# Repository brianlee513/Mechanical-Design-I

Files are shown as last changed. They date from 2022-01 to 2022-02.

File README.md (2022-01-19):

# Mechanical-Design-I
ME 370

The goal of this project is to design and build a four legged walker with two different mechanisms. 
More specifically, linkage design and cam follower design. With a single motor given, the four leggeed walker should be capable of walking 10m under 2 minutes.

The side view of the final design



Mechanism of the Rear Legs ( Cam Follower Design)



Mechanism of the Front Legs (Linkage Design)



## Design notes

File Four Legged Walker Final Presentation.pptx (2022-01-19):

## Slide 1

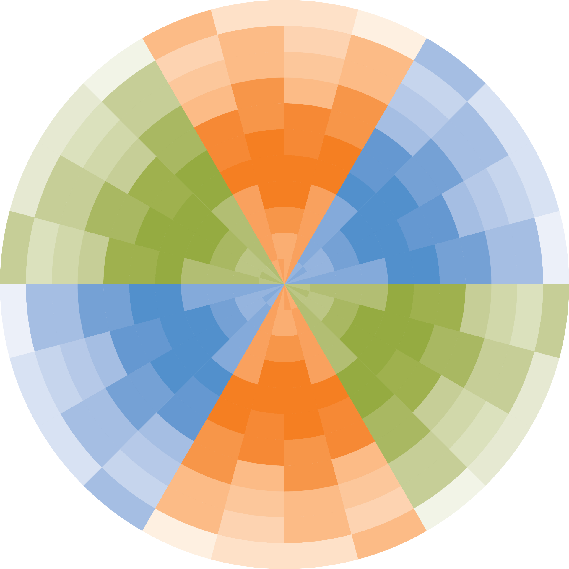
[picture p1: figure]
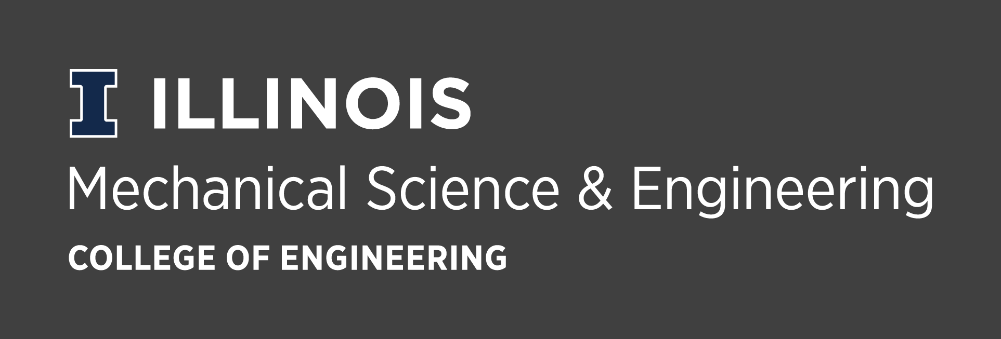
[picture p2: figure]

ME370
4-Legged Walker Final Report

Team 12:
Josh Stutzman, Marco Gasca, Brian Lee, Shubh Taneja
Section:
Date: 12/3/2021

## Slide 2

Overview

- 4 bar Linkage Design
- Slot Cam Design
- Power Source: 4 AA Batteries & DC Motor
- 2 Belts Transmit power
- 3 Gears in Total
( 30T Gear, 24T Gear )

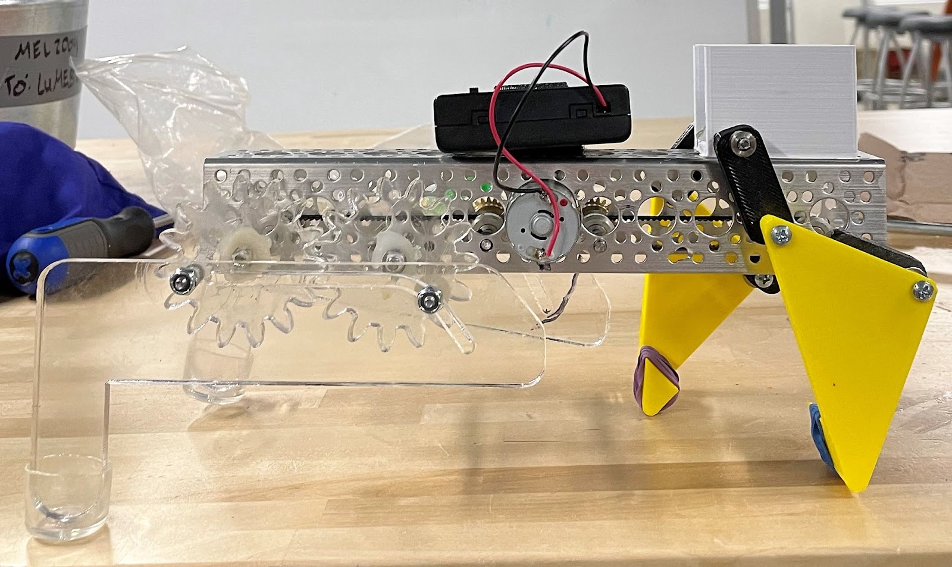
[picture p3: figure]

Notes: General Theme: legs closer to the u-base and have minimal parts to accomplish the goal.
Having many parts builds up movements creating unstable walker.

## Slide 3

Power Transmission Unit

Side View

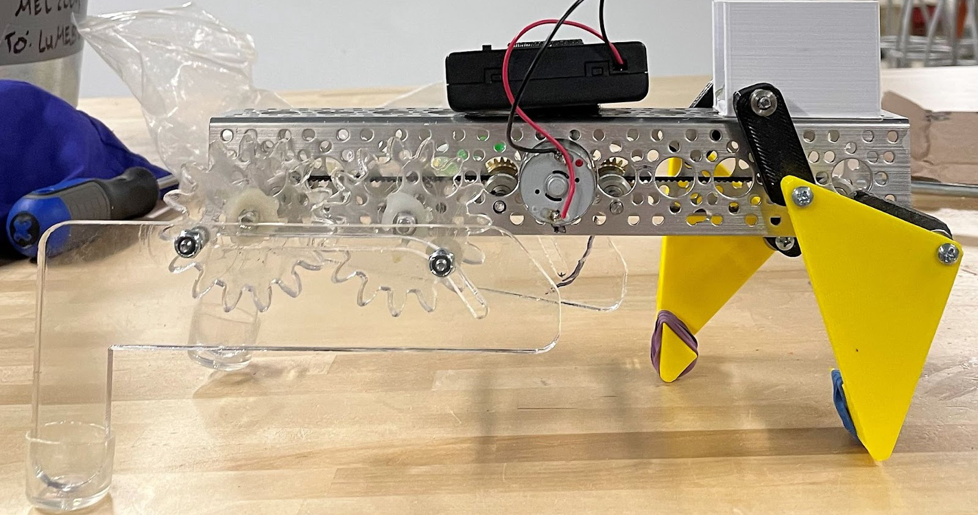
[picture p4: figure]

Rear Leg (Axial Translating Flat Form Closure)

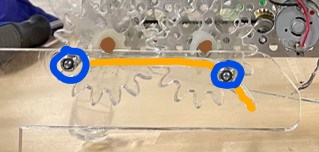
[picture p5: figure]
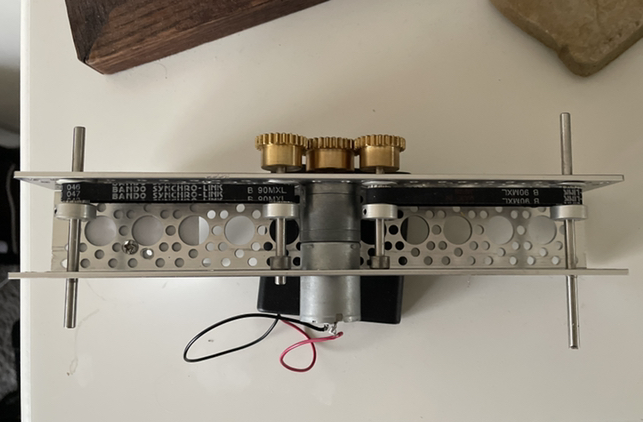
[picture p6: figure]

Bottom View 1

Bottom View 2

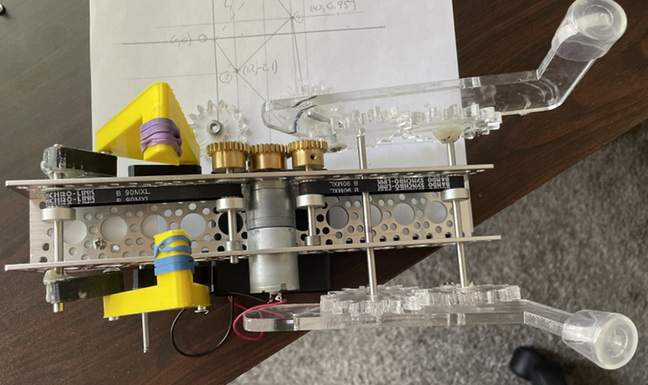
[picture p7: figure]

Front Leg

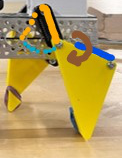
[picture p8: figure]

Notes: The transmission unit consists of one 30t gear, two 24t gears, two belts that transmit the rotational movement to the end of the u-base, and four shafts.
Rigid Link: provided the desired foot path, while keeping the legs closer to the u-base.
Cam-Follower: this type of design provided us to accomplish both vertical and horizontal motion of the leg at the same time.

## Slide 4

Foot Path

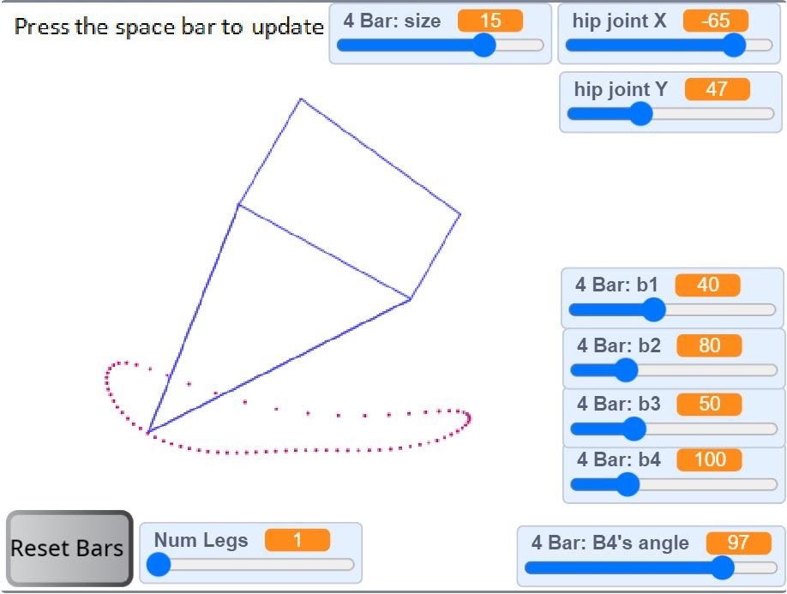
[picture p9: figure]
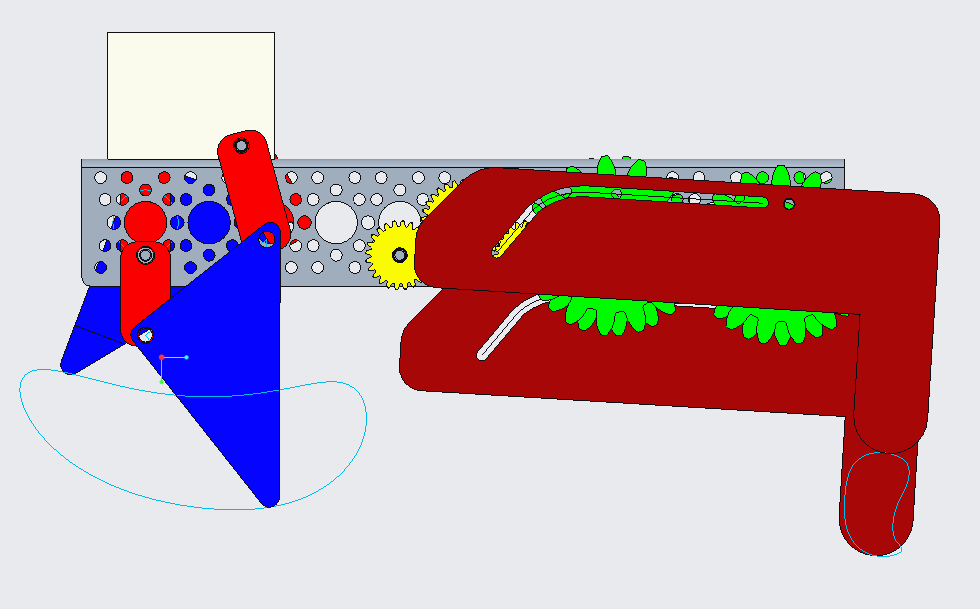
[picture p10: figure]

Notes: Front leg has some flaws where it’s a quick return.
The pros for the rear leg is that it is not a quick return. It makes the step very stable and uniform.

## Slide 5

Speed of the Walker

Load | 0g | 300g | 450g | 600g | 712.5g
RPM of DC Motor | 116.86 | 106.58 | 101.94 | 98.19 | 94.07
RPM 30T Gear | | | | | 94.07
RPM 24T Gear | | | | | 117.5828

- Step Size : Approximately 8 cm/rotation
- Calculated Speed : 13.7 cm/s
- Approximately 90s to complete 12m

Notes: From the DC motor lab, we calculated the approximated rpm for the motor, 30T gear, and 24t gear by applying the weight(712.5g) of the walker as the load.
Then calculated the actual speed of the walker. However, the actual speed of the walker differs quite significantly due to slipping and imbalance of the u-base creating the foot path to lose or make contact earlier than expected.

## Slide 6

PVA and DFA Analysis of Rigid Linkage Leg Animation

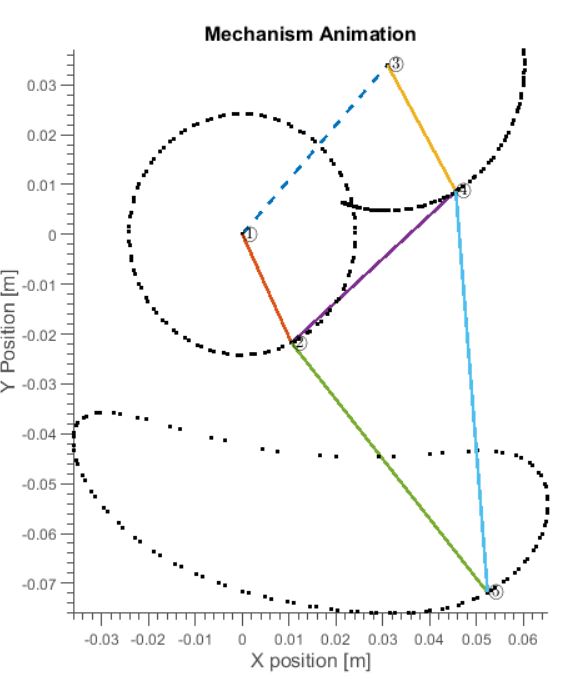
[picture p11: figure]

- Contact time- 60%
- Stride Length Ls – 8cm

Lift Phase

Contact Phase

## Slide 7

PVA and DFA Analysis of Rigid Linkage Leg

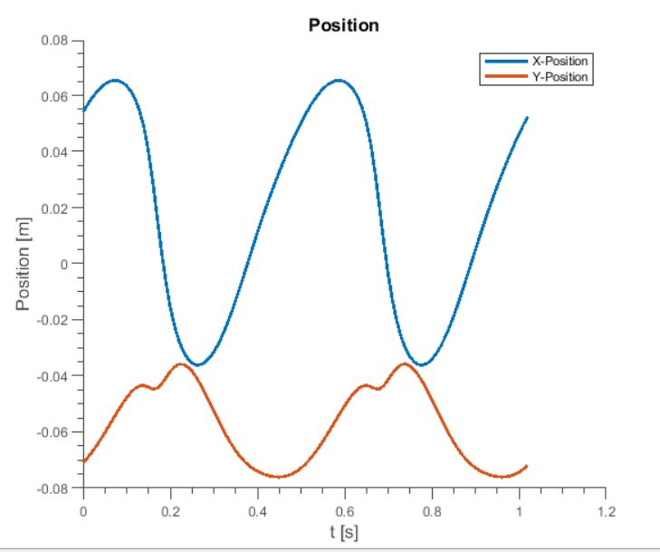
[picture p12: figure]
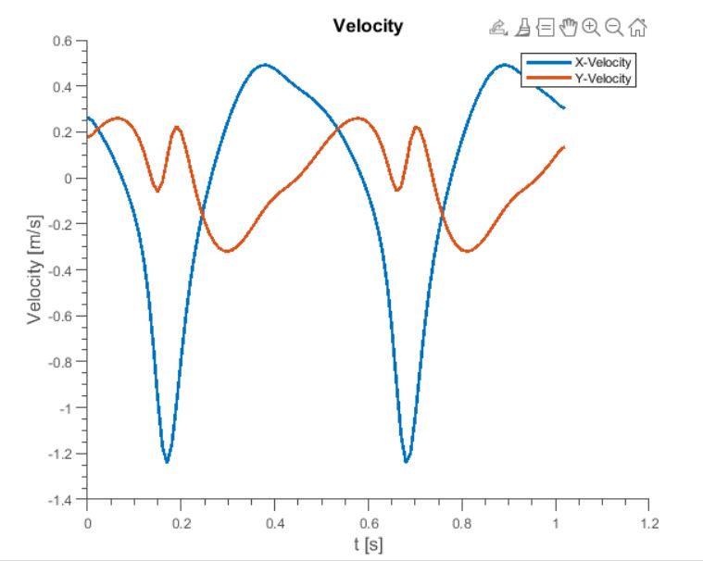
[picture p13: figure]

Contact Phase

Lift Phase

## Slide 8

PVA and DFA Analysis of Rigid Linkage Leg

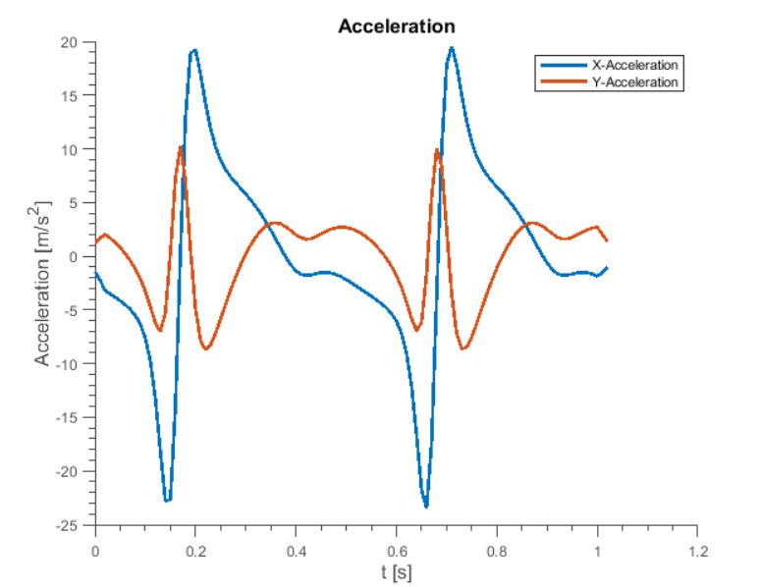
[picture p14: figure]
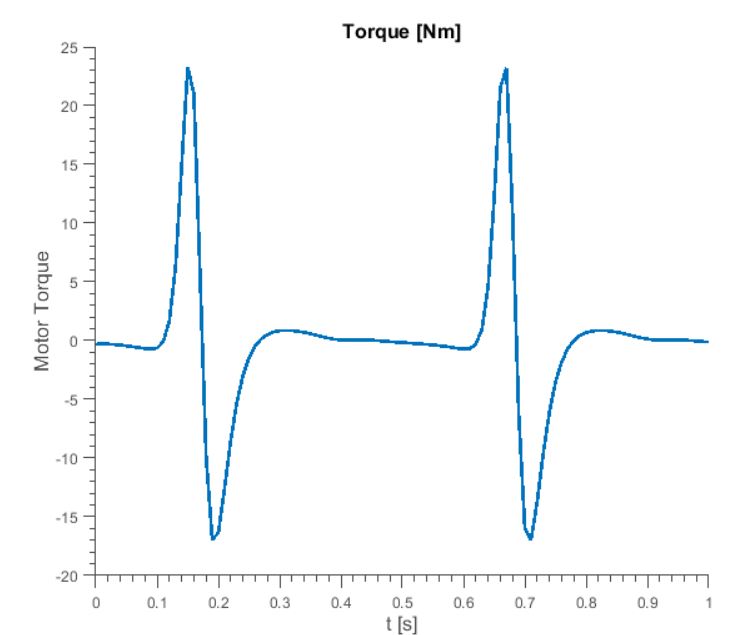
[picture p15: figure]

Contact Phase
Valid
Max Torque = -0.5Nm

Lift Phase
Invalid

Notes: Acceleration was abnormally high for some unknown reason. The torque was very low except for the spikes which can be ignored.

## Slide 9

Exploded View and Engineering Drawings

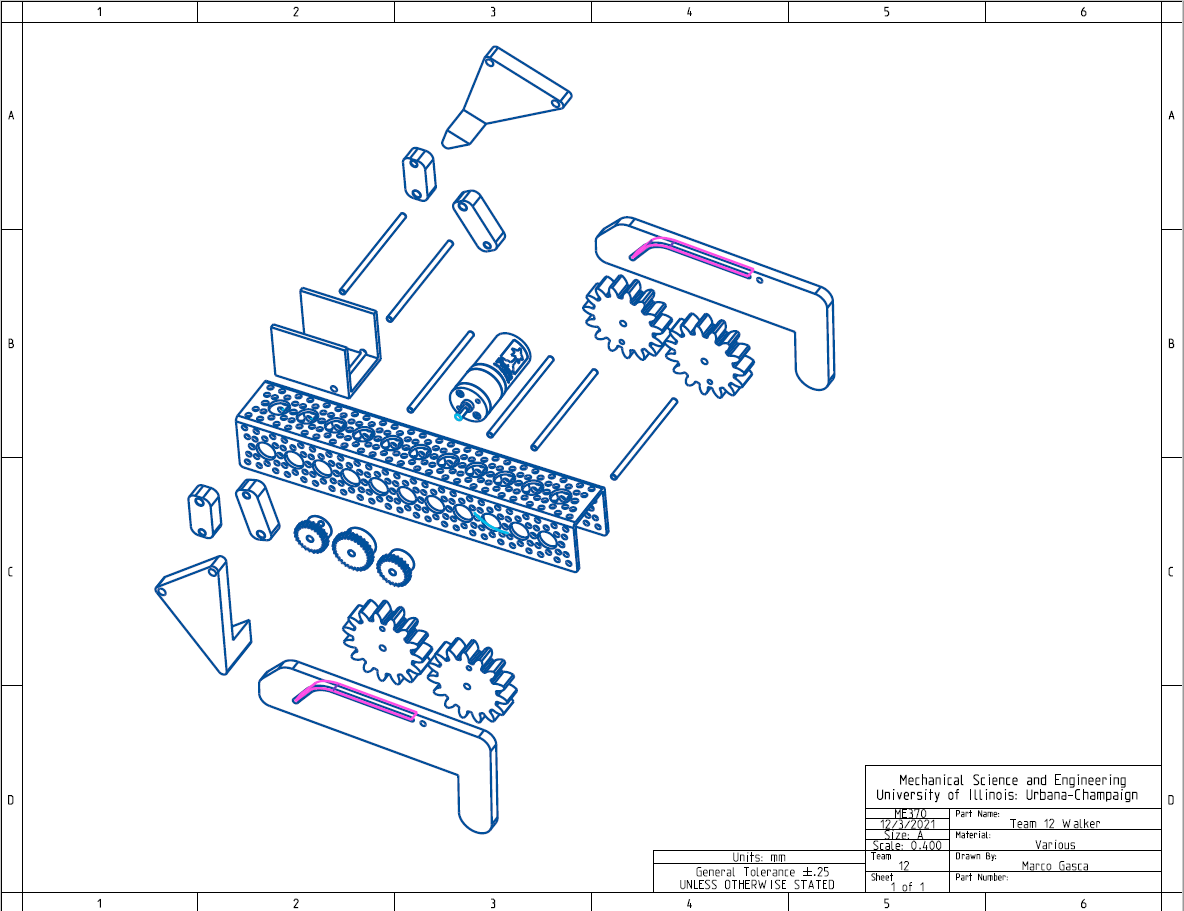
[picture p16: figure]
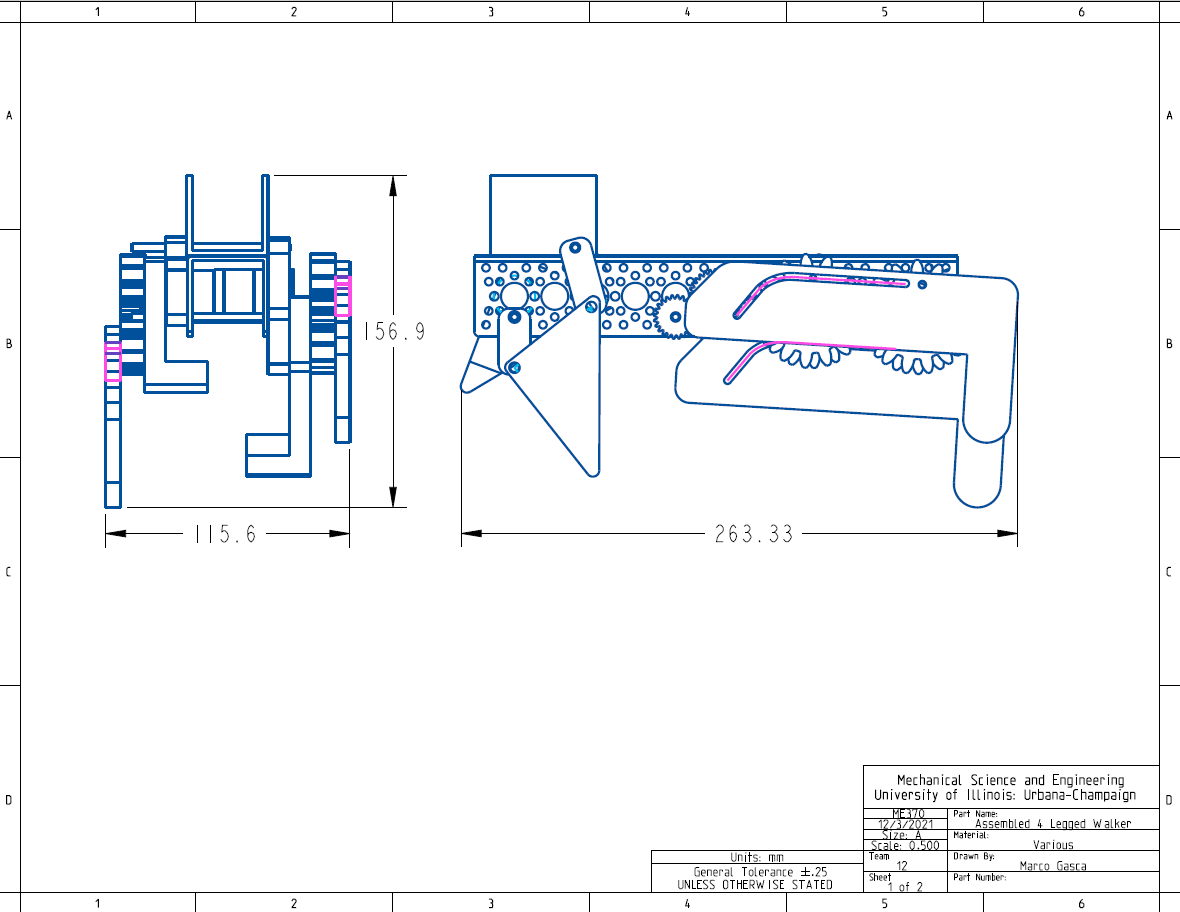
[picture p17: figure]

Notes: The transmission unit consists of one 30t gear, two 24t gears, two belts that transmit the rotational movement to the end of the u-base, and four shafts.

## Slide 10

Budget and Bill of Materials

Cost Breakdown
Part | Quantity | Unit Cost ($) | Total Cost ($) | Part | Quantity | Unit Cost ($) | Total Cost ($)
U-base | 1 | 8 | 8 | Allen Wrench 1.27 mm | 1 | 0.2 | 0.2
DC Motor | 1 | 20 | 20 | Allen Wrench 1.5 mm | 1 | 0.2 | 0.2
24 Tooth Gear | 2 | 23.4 | 46.8 | Sleeve Bearing | 1 | 0.6 | 0.6
30 Tooth Gear | 1 | 25.2 | 25.2 | #6-32 Coarse Nut | 6 | 0.32 | 1.92
Batteries and Accessories | 1 | 22 | 22 | #6-32 ½” Machine Screw | 2 | 0.21 | 0.43
Belt Gear 15 Tooth | 4 | 14.6 | 58.4 | #6-32 ¾” Machine Screw | 4 | 0.21 | 0.85
182 mm Belt | 2 | 5.5 | 11 | Barrel Nut and Screw ⅞” | 4 | 0.5 | 2
Shaft Collar | 14 | 1.7 | 23.8 | Acrylic Sheet 24” x 12” x ¼” | 1 | 20 | 20
150 mm Shaft | 2 | 1.2 | 2.4 | ¼” x 36” steel rod | 1 | 3.4 | 3.4
50 mm Shaft | 2 | 1 | 2 | ⅞” Clear Leg Tip | 2 | 0.7 | 1.41
73 mm Shaft | 1 | 0.6 | 1.2 | 3D Printed Leg | 63g | 0.03 | 1.89
#10 Washers | 4 | 0.04 | 0.16 | 3D Printed U-base Extension | 17g | 0.03 | 0.51

Sum | | 1 | 220.96 | | | 2 | 33.41
Total Cost | | | | | | 1 + 2 | 254.37

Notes: Most of the cost comes from the body of the walker- motor, gears, belts and batteries. The prototype legs themselves were very cheap and did not contribute much to the total cost. The total cost of the rocker is under budget, but enough of the budget was used to ensure that corners weren’t cut and a quality product was produced.

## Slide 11

Design Failures / Lesson Learned

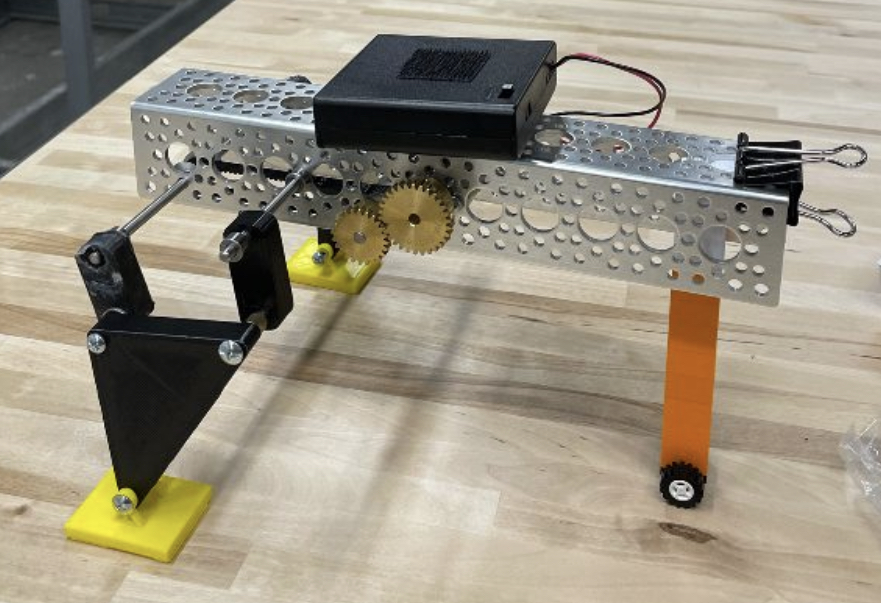
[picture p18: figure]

Linkage Design 1

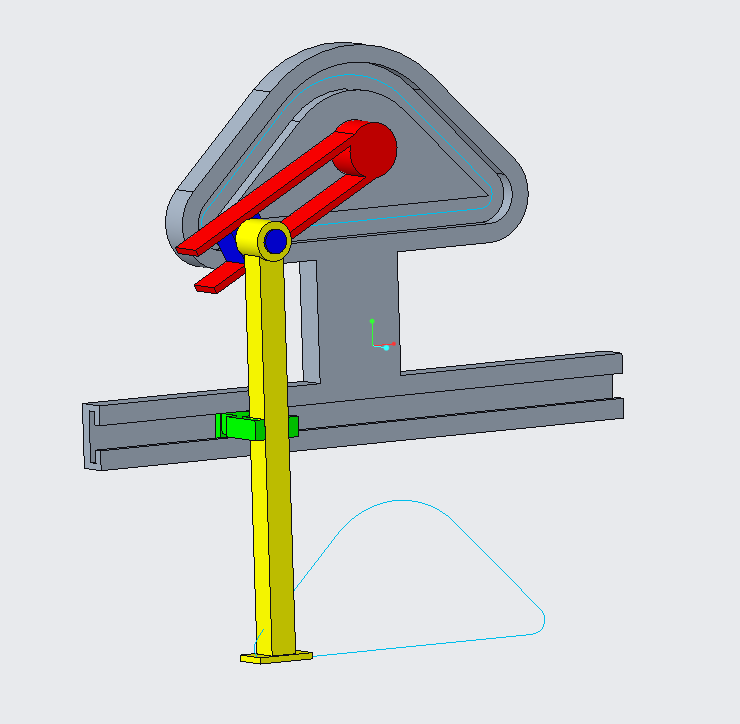
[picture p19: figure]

Cam Design 1

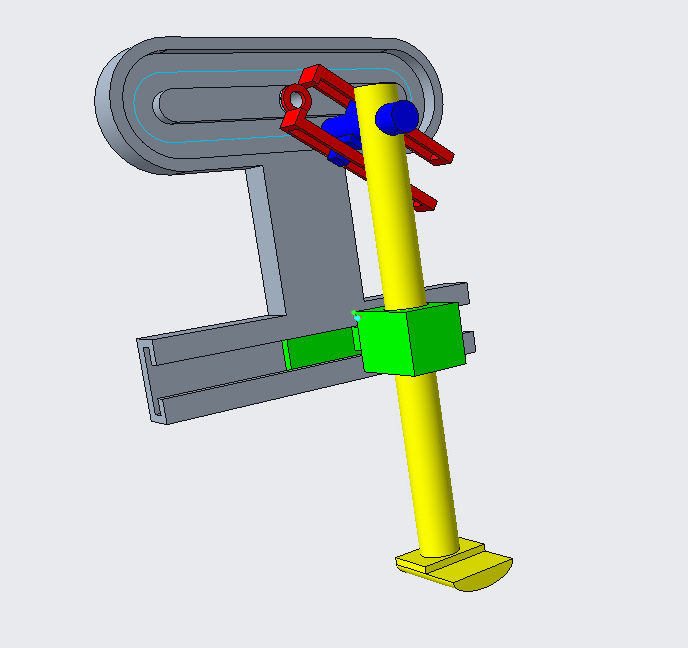
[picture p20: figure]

Cam Design 2

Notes: Design Iterations
Design1: The legs were too far out from the u-base. Single point contact for the rear wheel.
Cam Design 1:
Uncertainty over how the mechanism will behave at the sharp corners.
Nothing was holding the blue follower and the yellow leg to fall out of the slot.
The green clamp rotated as the blue follower lead the motion, making the mechanism to lock at one location
Cam Design 2:
Since the Red part is leading the motion, there was a delay in motion at the green slider. The delay created the yellow piece to be out of its perpendicular position to the ground.

Lesson Learned:
Designing: Considering fastening methods at the earlier stage
Manufacturing: Considering manufacturing challenges in 3d printing, long wait and tolerance issue
Testing: Considering the method of testing after manufacturing. Supply and the level of test we desire.
Right supply to keep one end for the u-base to maintain horizontal. The desired footpath was generated, but the foot was hitting the ground earlier than expected because the rear was lowered than the front.

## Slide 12

Progression Video

https://drive.google.com/file/d/1e48WqrADJp_-YnRn2FuT256TExa1mEri/view?usp=sharing

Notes: Just to be displayed on screen

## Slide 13

Team Contributions

- Design Review:
  - Marco Gasca: Measured possible hole to be utilized
  - Brian Lee: 3d modeling of the entire walker with the chosen design, Calculated the linkage
  - Josh Stutzman: Path generation for both legs
  - Shubh Taneja: Assisted in path generation
- Milestone 1:
  - Marco Gasca: 3D printed the CAD parts
  - Brian Lee: Create CAD model of all the linkage parts and designed linkage
  - Josh Stutzman: Assembled the linkage design, and tested
  - Shubh Taneja: Brainstormed and suggested possible linkage designs
- Milestone 2:
  - Marco Gasca: Create CAD model for the cam-follower design
  - Brian Lee: Assisted in creating cam-follower design, laser cut the parts, and tested the walker
  - Josh Stutzman: Assembled the cam-follower design, tested the walker, and assisted in design
  - Shubh Taneja: No contribution
- Deliverables 2 & 3:
  - Marco Gasca: CAD rendering and assembly engineering drawings (Part 4)
  - Brian Lee: Design description and analysis (Part 1)
  - Josh Stutzman: PVA and DFA analysis and budget and BOM (Parts 2 & 3)
  - Shubh Taneja: 1-minute video

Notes: Just to be displayed on screen

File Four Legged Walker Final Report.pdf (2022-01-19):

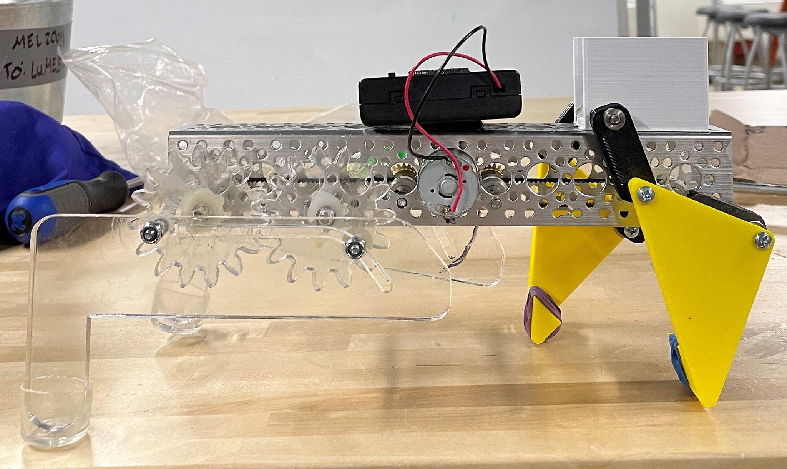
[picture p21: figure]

# Detailed Design Report

# ME 370 Section CB3 Team 12

Josh Stutzman, Marco Gasca, Brian Lee, Shubh Taneja

December 6, 2021

## Abstract

The purpose of this walker team project is to construct a four-legged walker that’s capable of completing twelve meters in under two minutes, with two legs being designed as linkage mechanisms, and two legs being designed as cam-follower mechanisms. In addition, the final dimensions of the walker must be within 30cm x 20cm x 20cm. The design process consists of initial sketching, path generating, prototyping, cad design, and manufacturing. 3D printing and laser cutting acrylic were used to fabricate parts that were not provided nor bought. Team 12 was capable of designing a four-legged walker that’s walkable with one set using a rigid linkage design and one set using a cam-follower design.

## Design Process

Project Goal:
The goal of this walker team project is to accomplish the purpose of the walker as described in the abstract in this report. During the design process, Team 12 made their goal to minimize parts to accomplish the same movement of the legs. Also, Team 12 had chosen their theme to mimic an army crawl motion or the movement of a gorilla to increase the stability of the walker.
Design Process:
The system requirements for this project are identical to the purpose of the walker team project described in the abstract. The user requirements that Team 12 have set were to have access to the batteries after assembly and to optimize the movement and stability. The design process of the linkage mechanism consisted of sketching possible linkage designs and measuring various hole distances on the u-base in order to see if the designs would fit. After this, the foot paths of the linkage designs were generated, and the process was reiterated until a desired path had been generated. Low-fidelity prototyping was conducted by mimicking the mechanism with cut chopsticks joined with a rubber band, and moving the modeled mechanism with our hands. Based on the measurements from the u-base, Team 12 used the linkage length ratio found during the footpath generation process to finalize the size of the linkages. In the case of the cam-follower design, Team 12 tried to mimic designs found on the internet through modeling the parts in CAD softwares and generating respective footpaths. The models were modified such that the cam-follower design’s step size and leg height closely resembled that of the rigid linkage leg. Figure 2 shows the candidate design we had during the design process. For the linkage design, Team 12 has chosen Linkage Design 1 in Figure 2, due to its simplicity compared to Linkage Design 2. In the case of cam-driven leg design, Team 12 chose Cam-Follower Design 2 after some design iterations in Cam-Follower Design1. The reason for this decision was made because Cam-Follower Design 1 was difficult to accomplish because there were many moving parts along with the green slider getting stuck in the slot. The synthesis process this walker utilized is 3D printing for the front leg and laser cutting ¼ inch acrylic. Team 12 believes that the team has met the overall goal of the project because the team has successfully designed a four-legged walker with two types of mechanism, a cam-driven leg and a linkage mechanism, within the design constraints of 30cm x 20cm x 20cm. Also, the user requirement was met by placing the battery on top of the walk, having access to the battery at all times. To add on, according to calculations, the walker should be able to complete 12m in 90 seconds.
To describe a few design iterations and failures, Figure 1 contains some designs Team 12 went through. Design Failure 1 had some unbalanced issue where the front legs were too far out of the u-base while having a point contact in the rear. This was both design failure and test failure causing the walker to rock. The second design failure occurred in the cam-driven leg. The design was full of flaws because there was not any force pushing the blue follower to be on track as well as the yellow leg to be attached to the blue follower. Also, the blue behavior of the blue follower was uncertain during the sharp corners, forcing the green clamp to halt in the slide. Team 12 modified the Design Failure 2 design to Design Failure 3. However, the modified green clamp would halt as well due to a rotating motion caused by the leg. This is because the motion is driven from the top which creates a slight delay in the movement of the entire yellow leg. Then the yellow leg is no longer perpendicular to the ground, creating the green part to rotate. Some of the lessons learned during this walker project are fastening methods and preparation of testing in the design phase. First, Team 12 had made design iterations for the fasteners to be placed. Also, failure caused by shaft collars detaching from some of the parts while testing. In the case of testing, Team 12 learned that the testing environment should be similar as possible to the condition in the CAD simulation. Team 12 had some difficulties during testing because the u-base was not leveled as in the simulation. This caused the footpath to not only be invalid but also make contact with the ground earlier than Team 12’s simulation. After the first iteration of the rigid link leg was 3D printed, it was realized that 3D printing components to be accurate within a fraction of a millimeter is very difficult. Many of our 3D printed components were inaccurate sized with holes being smaller than designed. After this realization, tolerancing was taken into account for hole size in the CAD models, with holes and slots being designed anywhere between 0.1 to 0.4 millimeters larger in diameter than the desired amount. Tolerancing is important for shaft holes and gear teeth.
Figure 3 shows the walker’s transmission unit which consists of one 30 tooth gear and two 24 tooth gears. The motion is transmitted to the end of the u-base by two belts. In the case of the front leg, the blue line rotates 360° acting as the crank. The orange line is the rocker (Figure 3 Front Leg). On the other end of the walker, the belt rotates the left acrylic gears which have a blue connecting point to the leg(Figure 3 Rear Leg). The left acrylic gear rotates the right acrylic gear, the right blue circle acts as a follower that follows the slot of the leg along the orange line (Figure 3 Rear Leg). Table 1 shows the data tabulated from DC motor Lab 8 was utilized to calculate the RPM of the motor and step size from the cad simulation. The step size was 8cm/rotation and the 24T gear had a 117 RPM which calculated the speed of the walker to be 13.7cm/s.

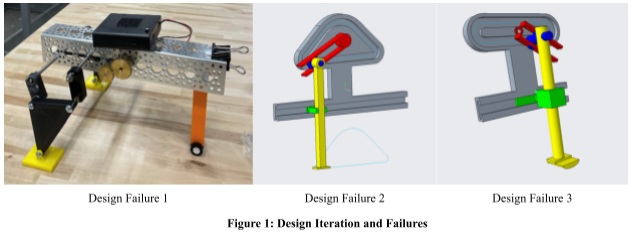
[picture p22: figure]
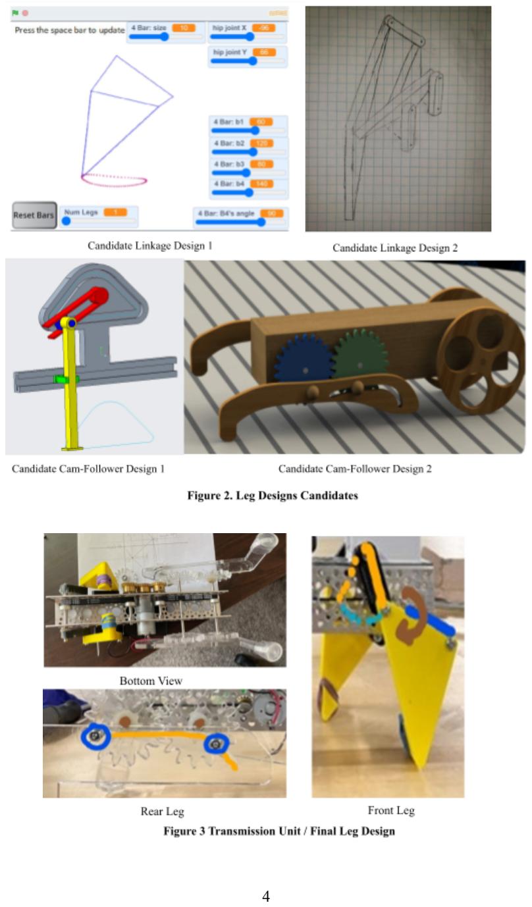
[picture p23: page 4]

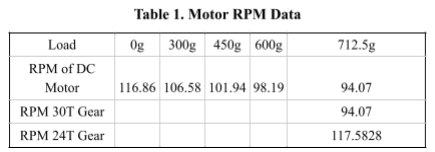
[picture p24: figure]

## Mechanism Analysis and Results


Looking at the figure above of the step animation of the walker and the position versus time graph in the figure below, it can be seen that the leg spends roughly 60% of the time in the contact phase, in which the foot is in contact with the ground, and 40% of the time in the lift phase, where the is no contact being made. In the figure below, the position versus time graph can be used to calculate the stride length, Ls

, as about 8cm. Again, looking at the torque versus time graph in the figure below, the max torque during the lift phase is -0.5 Nm, which occurs at 0.3 seconds. Since two legs will be on the ground at any given time, the actual torque required is doubled. The crank velocity used for this simulation was 117 rpm. This value was chosen using the motor load data from the DC motor lab during Week 7. The data was then extrapolated for the weight of the walker and the ratio of the large gear in the center to the smaller gear that drove the leg. Several things to note in the graphs in the figure below: Both the velocity and position graphs look normal and as expected. However, the acceleration in the x-direction is very high. The walker had a tendency to flip during tendency, and this analysis may have provided insight into the reason why. Furthermore, the torque graph’s results look relatively normal, as the torque in the crank is very low. Overall, the only big issue with the walker that can be seen from the analysis is the extremely high acceleration.


## Appendix A: Budget and BOM

Table 2. Final Prototype Budget and Bill of Materials

Cost Breakdown
Part | Quantity | Unit Cost ($) | Total Cost ($) | Part | Quantity | Unit Cost ($) | Total Cost ($)
U-base | 1 | 8 | 8 | Allen Wrench 1.3 mm | 1 | 0.2 | 0.2
DC Motor | 1 | 20 | 20 | Allen Wrench 1.5 mm | 1 | 0.2 | 0.2
24T Gear | 2 | 23.4 | 46.8 | Sleeve Bearing | 1 | 0.6 | 0.6
30T Gear | 1 | 25.2 | 25.2 | #6-32 Coarse Nut | 6 | 0.32 | 1.92
Batteries | 1 | 22 | 22 | #6-32 ½” Machine Screw | 2 | 0.21 | 0.43
Belt Gear 15 Tooth | 4 | 14.6 | 58.4 | #6-32 ¾” Machine Screw | 4 | 0.21 | 0.85
182 mm Belt | 2 | 5.5 | 11 | Barrel Nut and Screw ⅞” | 4 | 0.5 | 2
Shaft Collar | 14 | 1.7 | 23.8 | Acrylic Sheet 24” x 12” x ¼” | 1 | 20 | 20
150 mm Shaft | 2 | 1.2 | 2.4 | ¼” x 36” steel rod | 1 | 3.4 | 3.4
50 mm Shaft | 2 | 1 | 2 | ⅞” Clear Leg Tip | 2 | 0.7 | 1.41
73 mm Shaft | 1 | 0.6 | 1.2 | 3D Printed Leg | 63g | 0.03 | 1.89
#10 Washers | 4 | 0.04 | 0.16 | 3D Printed U-base Extension | 17g | 0.03 | 0.51

Sum | | | 220.96 | | | | 33.41
Total Cost | | | | | | | 254.37

Looking at the budget and bill of materials above, the final total cost of the walker came out to $254.37, which is just under the maximum allowable budget of $275. The majority of this cost came from the gears, motor, belts, batteries, and shaft collars. All of these parts were necessary to build a sturdy and working four-legged walker, and could not be reliably replaced through 3D printing or laser cutting. In comparison, the cost of the legs was nearly nothing, with the acrylic sheet being the most expensive component of the designed legs. It can be concluded that enough of the budget was used to ensure a quality product while still remaining comfortably under budget to demonstrate efficient designing. One potential area to save money, however, would’ve been with the acrylic sheets. Not all of the acrylic purchased was used, and purchasing multiple smaller portions as needed may have been more fiscally responsible.

## Appendix B: Assembly Drawings and BOM


## Appendix C: PVA and DFAAnalysis


The PVA analysis was done, shown in the two figures above, using two loops to encompass the leg. Links 4, 5, and 6 were rigid and formed a ternary link. To do this calculation, it was assumed that the crank velocity is constant, although this is most likely not the case. Treating the crank velocity as constant, however, allows us to use known values for the crank angular velocity and acceleration. To complete the DFA analysis shown below, there were several other assumptions that had to be made. It was assumed that the robot body was ground. In other words, it was strong enough to withstand the motor forces and torques. The second assumption was that the weight of the walker acted as a vertical normal force at the contact point of the foot and that the horizontal force on the foot was negligible. It was also assumed that the center of gravity of each link was at the midpoint of the respective link and that the effect of gravity on the links is negligible.


## Appendix D: Team Contributions and Signatures

Team Contributions
Design Review :
Marco Gasca: Measured possible hole to be utilized
Brian Lee: 3D modeling of the walker with the chosen design, calculated link lengths Josh Stutzman: Path generation for both legs
Shubh Taneja: Assisted in path generation
Milestone 1 :
Marco Gasca: 3D printed the CAD parts
Brian Lee: Created CAD models for all of the linkage parts and designed linkage Josh Stutzman: Assembled and tested the linkage design
Shubh Taneja: Brainstormed ideas for walker design
Milestone 2 :
Marco Gasca: Created CAD models and drawings for the cam-follower design and 3D printed parts
Brian Lee: Assisted in creating the cam-follower design, laser cut parts, and tested the walker
Josh Stutzman: Assembled, tested, and assisted in the design of the cam-follower leg Shubh Taneja: No contribution
Deliverables 2 & 3:
Marco Gasca: CAD rendering and assembly, and engineering drawings (Part 4) Brian Lee: Design description and analysis (Part 1)
Josh Stutzman: PVA and DFA analysis, budget, and BOM (Parts 2 & 3)
Shubh Taneja: 1-minute video
Academic Integrity Statement
I, Josh Stutzman, hereby agree to follow all academic integrity policies while producing
this report. In addition to my original contributions, I have read through this entire report and certify that all materials are correct and unplagiarized.
Signature: Joshua Stutzman
Date: 11/27/2021
I, Brian Lee, hereby agree to follow all academic integrity policies while producing
this report. In addition to my original contributions, I have read through this entire report and certify that all materials are correct and unplagiarized.
Signature: Brian Lee
Date: 11/28/2021
I, Shubh Taneja, hereby agree to follow all academic integrity policies while producing
this report. In addition to my original contributions, I have read through this entire report and certify that all materials are correct and unplagiarized.
Signature: Shubh Taneja
Date: 12/2/2021
I, Marco Gasca, hereby agree to follow all academic integrity policies while producing this report. In addition to my original contributions, I have read through this entire report and certify that all materials are correct and unplagiarized.
Signature: Marco Gasca
Date: 12/2/2021

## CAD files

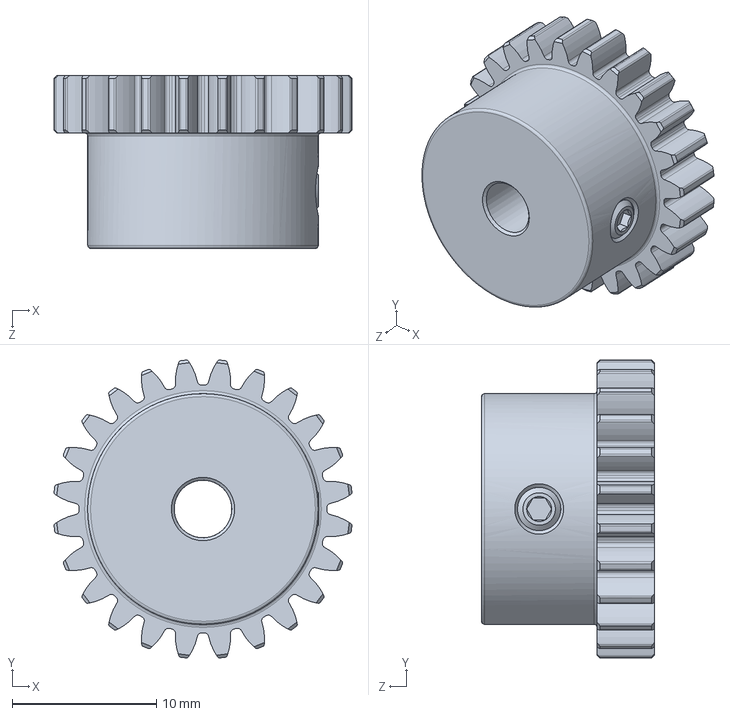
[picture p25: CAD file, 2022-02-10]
Four Legged Walker Cad/Four Legged Walker CAD_one_leg/2664N444_Metal Gear - 20 Degree Pressure Angle.SLDPRT
20.7 x 20.7 x 12.0 mm

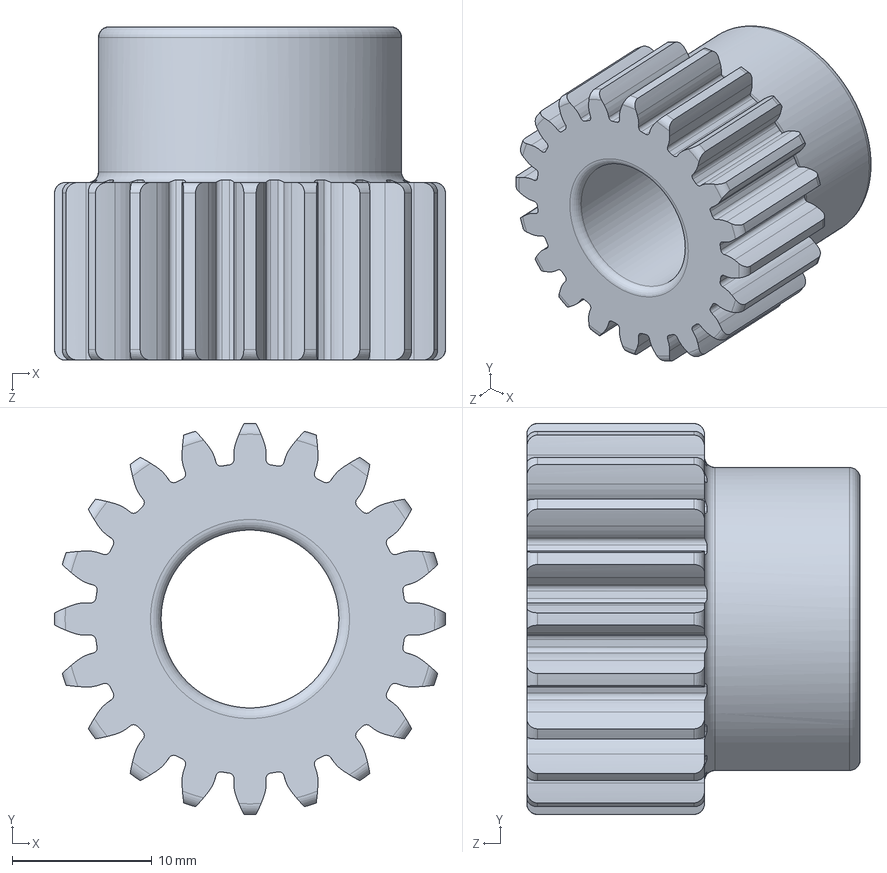
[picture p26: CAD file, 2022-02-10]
Four Legged Walker Cad/Four Legged Walker CAD_one_leg/5172T62_Metal Gear - 20 Degree Pressure Angle.SLDPRT
27.9 x 27.9 x 23.8 mm

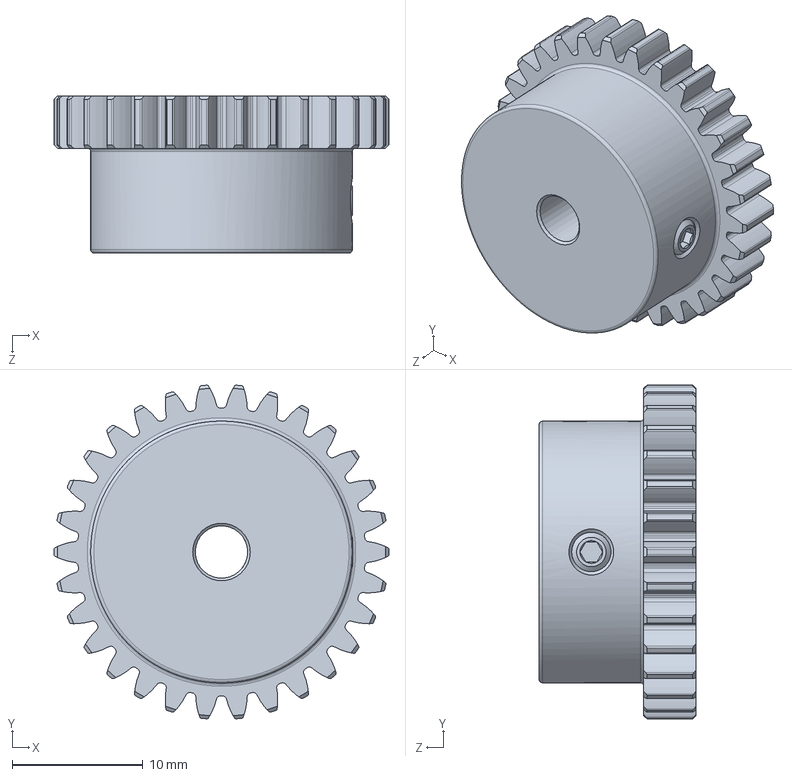
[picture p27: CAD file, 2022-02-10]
Four Legged Walker Cad/Four Legged Walker CAD_one_leg/2664N454_Metal Gear - 20 Degree Pressure Angle.SLDPRT
25.6 x 25.5 x 12.0 mm
